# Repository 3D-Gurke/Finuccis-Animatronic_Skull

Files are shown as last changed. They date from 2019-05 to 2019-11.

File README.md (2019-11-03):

# 3D-Gurke
3D printable mechanic for animatronic skull (Halloween)

This project was inspired by  www.youtube.com/watch?v=b6z9ToMeCnw

When I found out, how expensive even only one animated skull including animatronic kits was, I decided to use my 3D printer 
to produce my own animatronic skull.
I live in Germany and I was unable to obtain the Lindberg skull in Europe, for which many animatronic kits are available.
Therefore, I looked for an available and cheap alternate skull an I found a skull model named XC-104, produced in China 
with worldwide availabilty. It is pretty heavy with its 1,2 kg but it works fine after some amendments.
Inside the skull a lot of material needs to be removed with a dremel tool. This takes about 1/2 hour and it is pretty messy.
If you accidently take away too much and you create a hole, who cares? 
It is supposed to be a rotten skull, ain't it?
Especially the material inside the skull from nose downward towards the upper jaw needs to be removed to make space for the eyes 
animatronic board. It needs to be fit in perfectly or it will interfere with the skull servo board. It is basically a press fit.
The lower jaw (mandible) is linked to the skull by two cable straps on each joint. I will include schematics.
The animatronic is commanded by a cheap Arduino nano clone from China. 4 EUR each. 
This special Arduino has one flaw though, if steering servos, the servos cannot run on the same power supply (directly) as the arduino.
Therefore a cheap voltage DC DC converter (<1 EUR) was used. The Arduino can run on 12V directly, the servos are running on 5V.
In this configuration, everything runs perfectly.
This project is still in progress, as especially the programming has not been done except for a small test program.
The programming must be on a time code to syncronise the movement of the jaw to any audio file. In my case: 3 skulls singing
the Ghotbusters song. Therefore I need to syncronise 3 skulls with one master Arduino which will be starting the 3 skulls syncronously
and will be also steering the sound file and lighting effects. This will be done in the future however.
I am an absolute beginner in programming ARDUINO and what I present here is mostly copied from various net sources. 
It works so far, but as the project is not finished as yet, it is far from perfection or even elegance, 
so do not massacre me for the imperfect code, please  !  :-)
Each skull must be individually tested on each servo for the physical movement limits- I will include the test program as well.
I used the cheapest servos available from China. Servo MG945 & SG90. These do not center correctly and every time you hit a specific angle defined in the program, the servos end up in another position near by. Absolute unacceptable if used in an RC model, for a project like this, they do okay.
I have not specifically calculated the cost of a complete skull, but I would estimate 1 skull with servos and Arduino to be 
below 100 EUR. 
A pretty attractive price for an animatronic 3 axis skull with RGB lighted 2 axis eyes.
All hole measures of the printable parts have been chosen small so you can drill the holes to the dimension you need.
This way you can easily convert from metric to imperial measure. For instance: The tube for the eyes servo board to connect to the center eye ball is 4mm or approximately 1/6 inch. You will have to drill the holes in the board and the center eye ball accordingly.

Video-Tutorials this project: https://www.youtube.com/watch?v=9NNKajxI0-s&list=PLTyc4D895PUEJc8eNipVYug8fxN45OCBS

Final Installation, as run on Oct 31st 2019 : https://www.youtube.com/watch?v=-8c9RkCJJGA

Please find all necessary files in the folders.

You may remix as you see fit. Have fun und viel Glück!

Glück auf!

3D-Gurke

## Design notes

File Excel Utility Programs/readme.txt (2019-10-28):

The Excel File "INO Change Code Generator" will help you to create and adjust the time line.
"Arduino Code Translator"  is a generic translator program to convert my Ghostbusters skull programs to your skull's limits.
"Arduino Code Translator_ALPHA" is the same program preset with the ALPHA skull time line.
"Arduino Code Translator_BETA" is the same program preset with the BETA skull time line.
"Arduino Code Translator_GAMMA" is the same program preset with the GAMMA skull time line.

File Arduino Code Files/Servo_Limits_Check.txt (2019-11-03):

#include <VarSpeedServo.h>
#include <Adafruit_NeoPixel.h>

// Servo 
VarSpeedServo servo1;   // NOD
VarSpeedServo servo2;   // SHAKE              
VarSpeedServo servo3;   // TILT
VarSpeedServo servo4;   // JAW
VarSpeedServo servo5;   // Eye X
VarSpeedServo servo6;   // Eye Y

const int servoPin1 = 3;
const int servoPin2 = 5;
const int servoPin3 = 6;
const int servoPin4 = 9;
const int servoPin5 = 10;
const int servoPin6 = 11;

// NeoPixel
#define PIN  2
#define NUMPIXELS 2
Adafruit_NeoPixel eyes = Adafruit_NeoPixel(NUMPIXELS, PIN, NEO_GRB + NEO_KHZ800);

void setup() 
{

eyes.begin();

// all servos 90°

servo1.attach(servoPin1);
servo1.write(90,30,false); 
servo2.attach(servoPin2);
servo2.write(90,30,false); 
servo3.attach(servoPin3);
servo3.write(90,30,false); 
servo4.attach(servoPin4);
servo4.write(90,30,false);
servo5.attach(servoPin5);
servo5.write(90,30,false); 
servo6.attach(servoPin6);
servo6.write(90,30,false); 

eyes.setPixelColor(0, eyes.Color(0,0,0));
eyes.setPixelColor(1, eyes.Color(0,0,0)); 
eyes.show();
}
void loop() 
{
eyes.setPixelColor(0, eyes.Color(0,100,0));
eyes.setPixelColor(1, eyes.Color(0,100,0)); 
eyes.show();
servo1.write(90,30,false);        // eyes light green when servo in 90° neutral
delay(3000);
eyes.setPixelColor(0, eyes.Color(100,0,0));
eyes.setPixelColor(1, eyes.Color(100,0,0)); 
eyes.show();
servo1.write(100,30,false);       // eyes light red when servo in tests limit
delay(3000);
eyes.setPixelColor(0, eyes.Color(0,100,0));
eyes.setPixelColor(1, eyes.Color(0,100,0)); 
eyes.show();
servo1.write(90,30,false);        // eyes light green when servo in 90° neutral
delay(3000);
eyes.setPixelColor(0, eyes.Color(100,0,0));
eyes.setPixelColor(1, eyes.Color(100,0,0)); 
eyes.show();
servo1.write(80,30,false);       // eyes light red when servo in tests limit
delay(3000);
eyes.setPixelColor(0, eyes.Color(0,100,0));
eyes.setPixelColor(1, eyes.Color(0,100,0)); 
eyes.show();
servo1.write(90,30,false);        // eyes light green when servo in 90° neutral

}

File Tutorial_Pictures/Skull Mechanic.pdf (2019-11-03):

### Aufbau der Anlenkmechanik für Halloween Totenkopf Schematic of linkage assembly for halloween skull

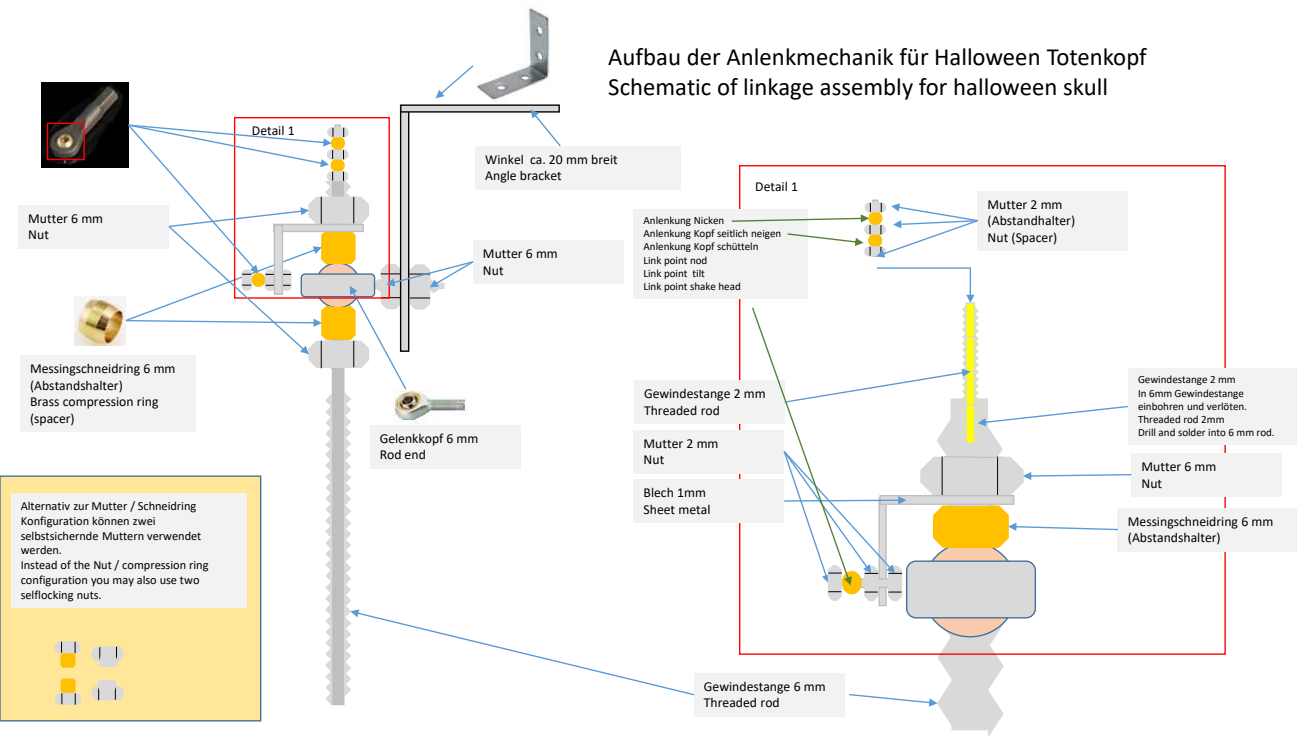
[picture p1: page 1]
Gewindestange 6 mm Threaded rod; Gelenkkopf 6 mm Rod end; Mutter 6 mm Nut; Detail 1; Mutter 2 mm Nut; Gewindestange 2 mm Threaded rod; Blech 1mm Sheet metal; Mutter 2 mm (Abstandhalter) Nut (Spacer); Messingschneidring 6 mm (Abstandshalter)

Winkel ca. 20 mm breit
Angle bracket

Anlenkung Nicken
Anlenkung Kopf seitlich neigen
Anlenkung Kopf schütteln
Link point nod
Link point tilt
Link point shake head

Messingschneidring 6 mm
(Abstandshalter)
Brass compression ring
(spacer)

Gewindestange 2 mm
In 6mm Gewindestange
einbohren und verlöten.
Threaded rod 2mm
Drill and solder into 6 mm rod.

Alternativ zur Mutter / Schneidring
Konfiguration können zwei
selbstsichernde Muttern verwendet
werden.
Instead of the Nut / compression ring
configuration you may also use two
selflocking nuts.

# Detail Anlenkung / Detail Linkage

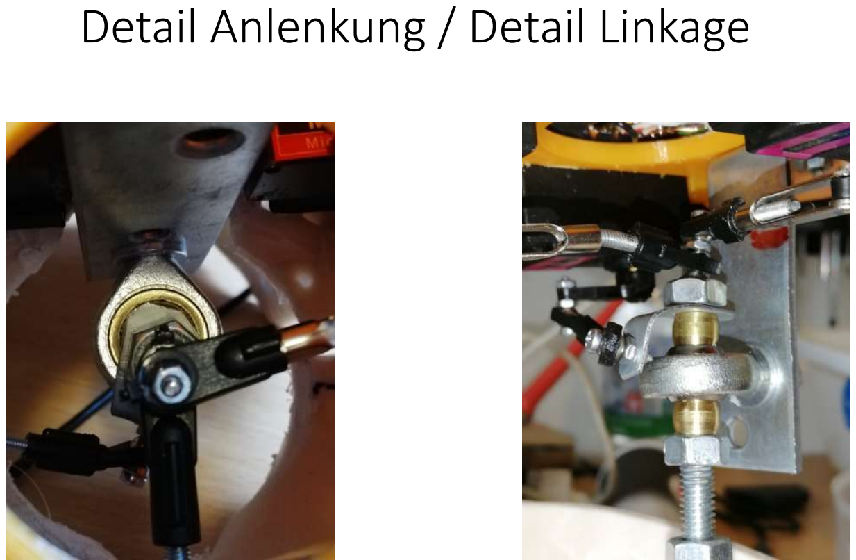
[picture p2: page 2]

### 19 x 15 x 21 cm , 1.16 kg Skull Medical Model XC-104 (China)

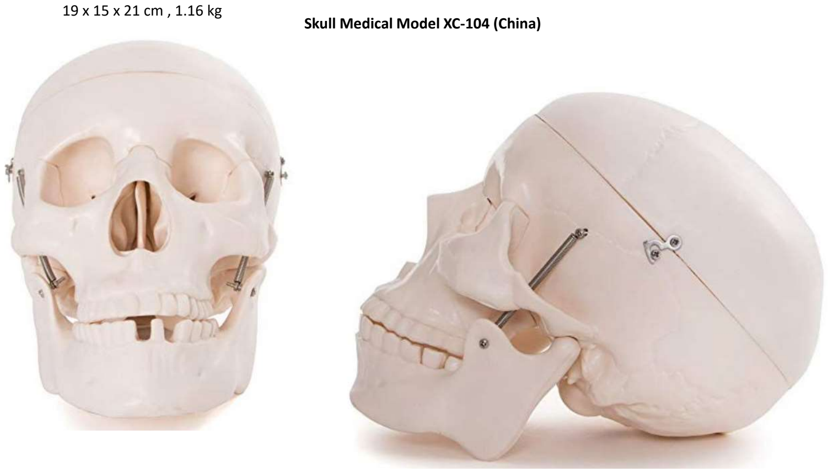
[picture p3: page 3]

# Servohalter Bestückung Servo board assembly

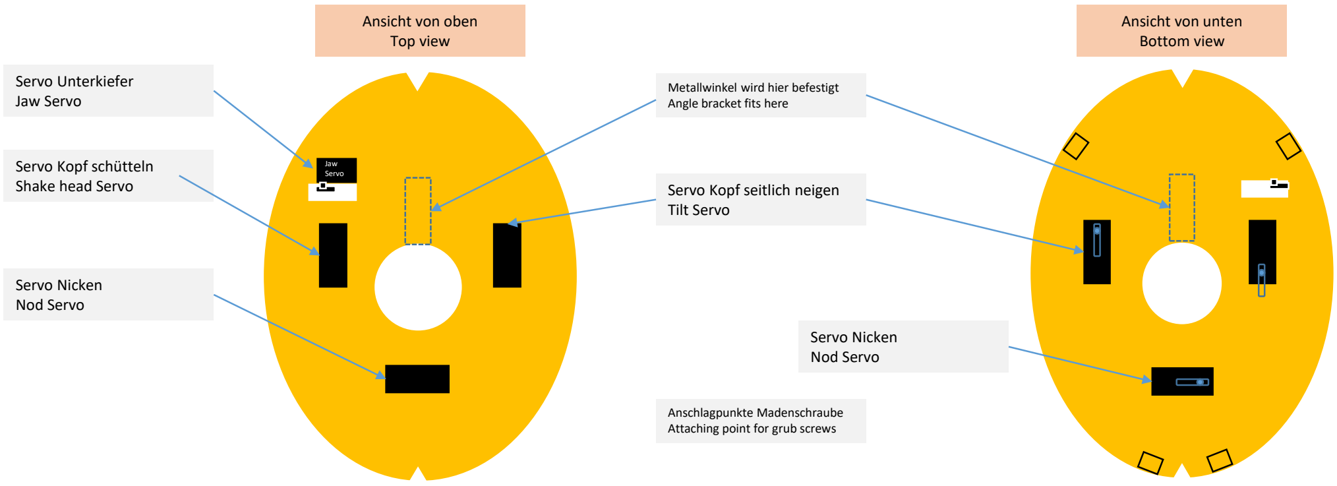
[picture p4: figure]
Jaw Servo; Servo Unterkiefer Jaw Servo; Servo Kopf schütteln Shake head Servo; Servo Nicken Nod Servo; Servo Kopf seitlich neigen Tilt Servo; Ansicht von oben Top view; Ansicht von unten Bottom view; Metallwinkel wird hier befestigt Angle bracket fits here; Anschlagpunkte Madenschraube Attaching point for grub screws

# Materialliste Skull

Schädel (Typ XC-104) | 1 stck | (Skull)
Skull Servo Board | 1 stck 3D Druck | (3D print)
Servo holder | 1 stck 3D Druck | (3D print)
Gewindestange 6 mm | 1 stck | (Threaded rod)
Gewindestange 2 mm | 3 stck | (Threaded rod)
Mutter 6 mm | 5 stck | (Nut)
Mutter 2 mm | 6 stck | (Nut)
Servo Kugelkopf 2 mm | 6 stck | (Servo link rod end)
Gelenkkopf m Gewindestange 6mm 1 stck | (Rod end)
Messingschneidring 6 mm | 2 stck oder 6 mm selbstsichernde Mutter 2 stck (Brass compression ring or 2 ea selflocking nut)
Metallwinkel 20 mm | 1 stck | (Angle bracket)
1 mm Blech | Reststück | (Sheet metal piece scrap)
Servo MG945 | 3 stck | (Servo, China ware)
Servo SG90 | 1 stck | (Servo, China ware)
Arduino USB Nano V3.0 | 1 stck | (Arduino)
Step-Down-Schaltregler | 2 stck | (Step down buck converter)
Lochrasterplatine (10 x 20 Löcher) | 1 stck | (Blank circuit board 10 by 20 holes)
Madenschraube 4mm | 4 stck | (Grub screw)

# Materialliste Eyes Board

Eyes Board: | 1 stck 3D Druck | (Eyes Board:, 3D print)
Eye Center Ball | 2 stck 3D Druck | (Eye Center Ball | , 3D print)
Eye Ball | 2 stck 3D Druck | (Eye Ball, 3D print)
Verbinder | 1 stck 3D Druck | (Link bar, 3D print)
Servo SG90 | 2 stck | (Servo, China ware)
Draht 1 mm | 10 cm | (Metal wire, 1 mm)
Rohr 4 mm aussen (z.B Plastik) | 10 cm | (Tube, 4 mm outer diameter plastic)
LED Typ WS2812 5050 (4 pin) | 2 stck | (LED, China ware)

2 mm Schrauben / Muttern / Unterlegscheiben / Kabelbinder / Steckverbinder / Lochrasterplatine / Kupferlackdraht
( 2mm screws / nuts / washers / cable straps / male & female pins for circuit boards / circuit board / magnet wire)

# Platine Oberseite / Circuit Board Top ViewZ 5V ¹²V LEDs Eyes

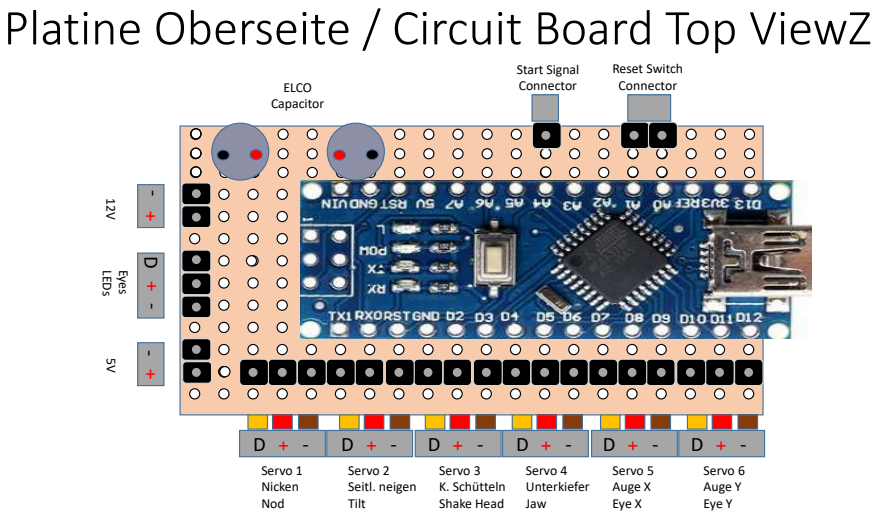
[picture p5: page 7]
Servo 1 Nicken Nod; Servo 2 Seitl. neigen Tilt; Servo 3 K. Schütteln Shake Head; Servo 4 Unterkiefer Jaw; Servo 5 Auge X Eye X; Servo 6 Auge Y Eye Y; Reset Switch Connector; Start Signal; ELCO; Connector; Capacitor

# Platine Oberseite / Circuit Board Top View

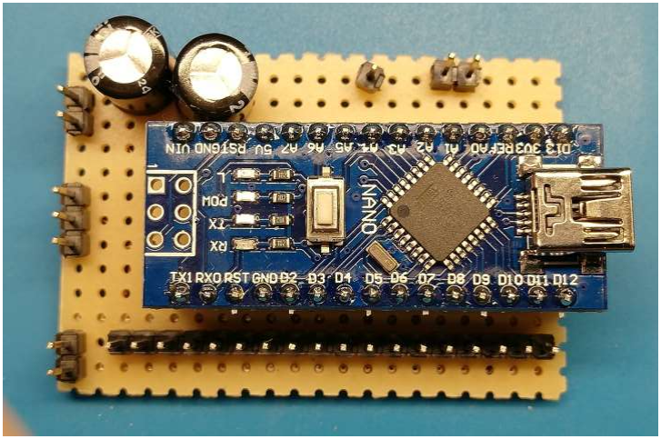
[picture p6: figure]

# Platine Unterseite/ CB Bottom View 5V 9V LEDs Eyes

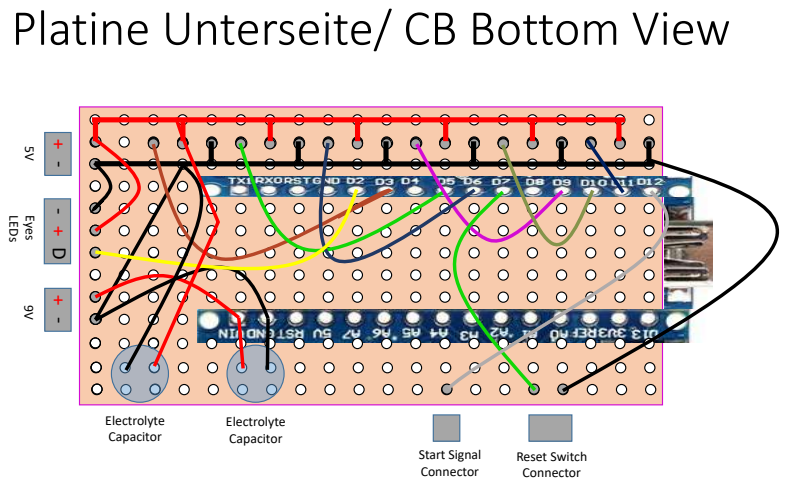
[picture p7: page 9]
Reset Switch Connector; Electrolyte Capacitor; Start Signal Connector

# Platine Unterseite/ CB Bottom View

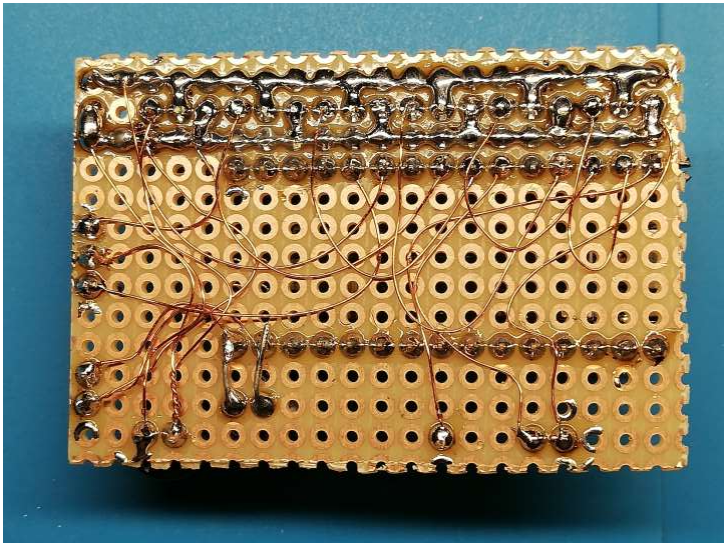
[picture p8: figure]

# Elektronische Schaltung Electronics Circuit

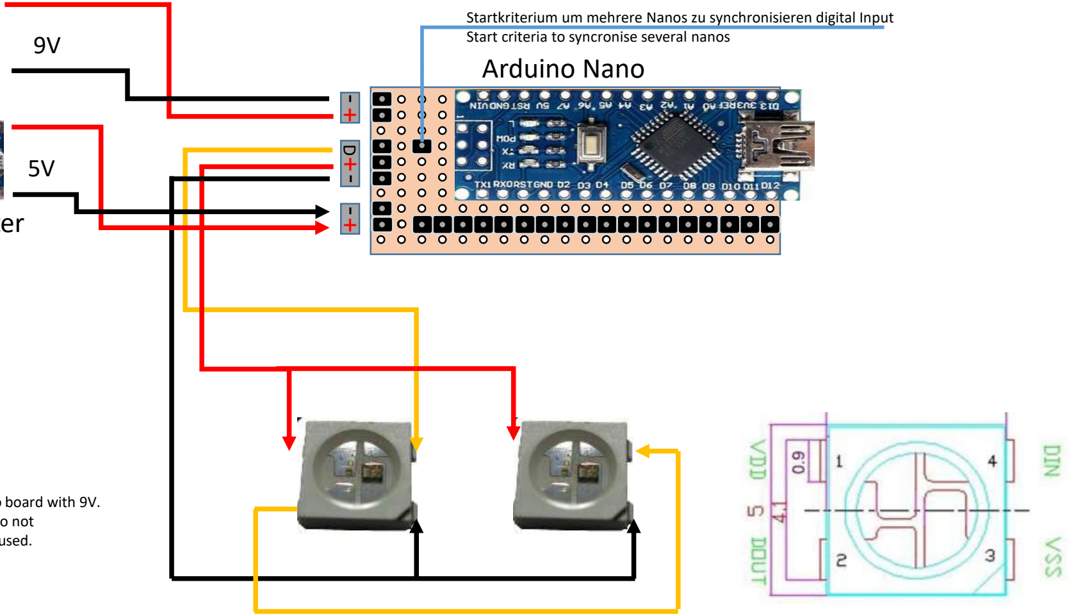
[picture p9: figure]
Arduino Nano

### Voltage Converter

Startkriterium um mehrere Nanos zu synchronisieren digital Input Start criteria to syncronise several nanos
Power Supply | 9V
12 V

Changed assembly:
Use a second step down voltage converter to power the Arduino board with 9V. When testing / programming, I found that some Arduino Nano do not
work correctly when only one step down voltage converter was used.
In this configuration, there were no more issues.

### Voltage Converter

!

# Servo Board Eyes/ Eye Board Assy

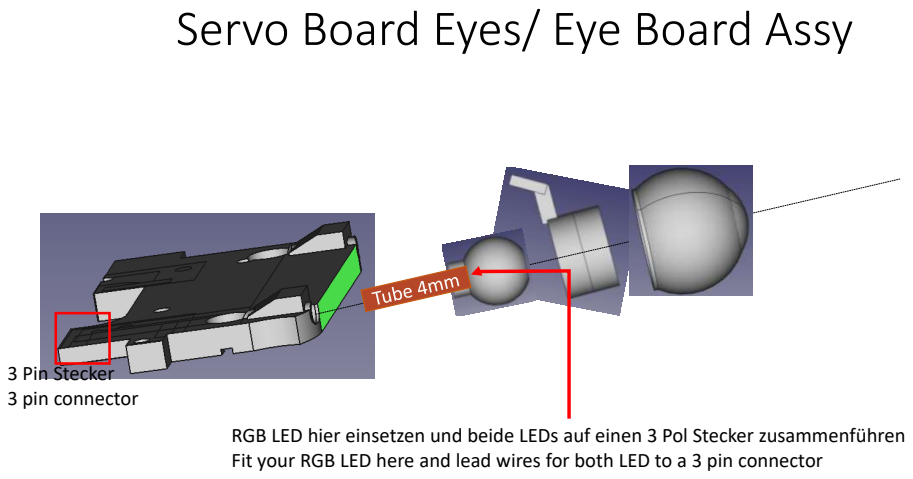
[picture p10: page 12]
3 Pin Stecker 3 pin connector

RGB LED hier einsetzen und beide LEDs auf einen 3 Pol Stecker zusammenführen
Fit your RGB LED here and lead wires for both LED to a 3 pin connector

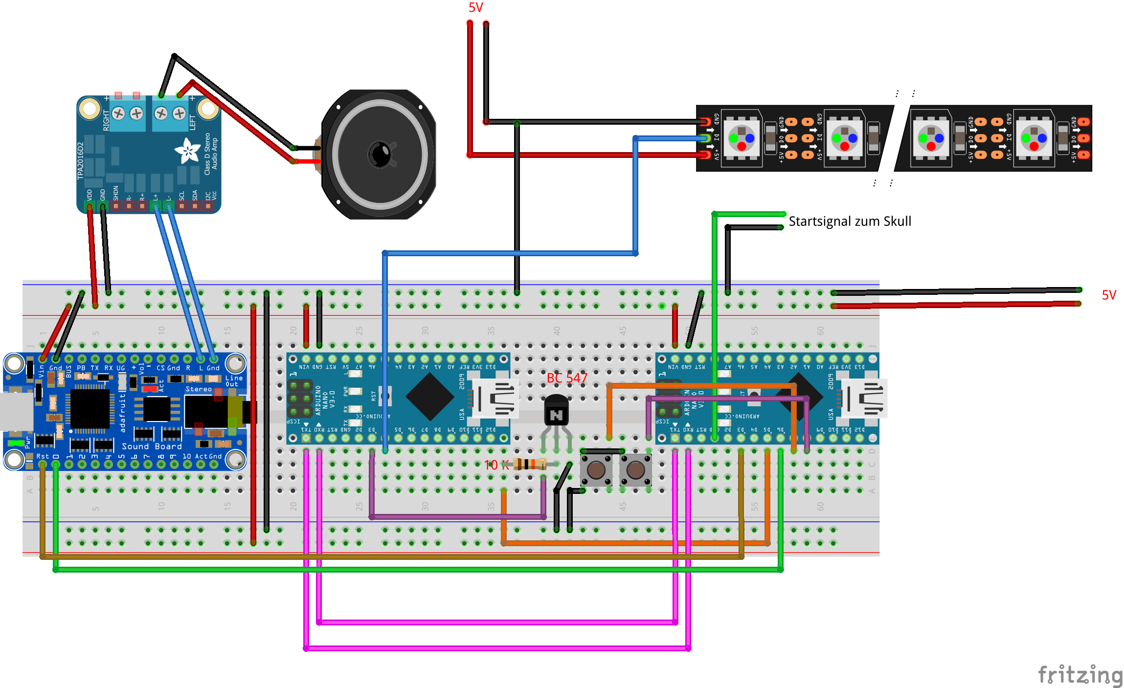
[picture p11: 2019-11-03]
Tutorial_Pictures/MASTER_BREAD_BOARD_schematic.png

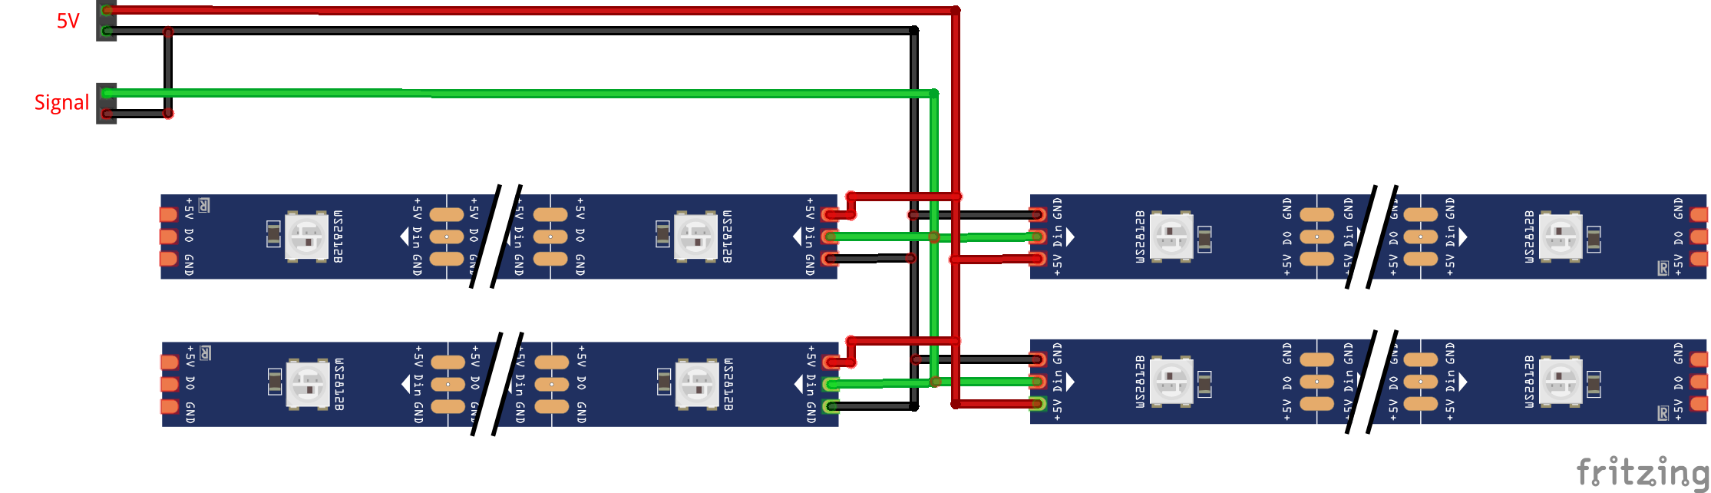
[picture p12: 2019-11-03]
Tutorial_Pictures/MASTER_LED_STRIP_schematic.png

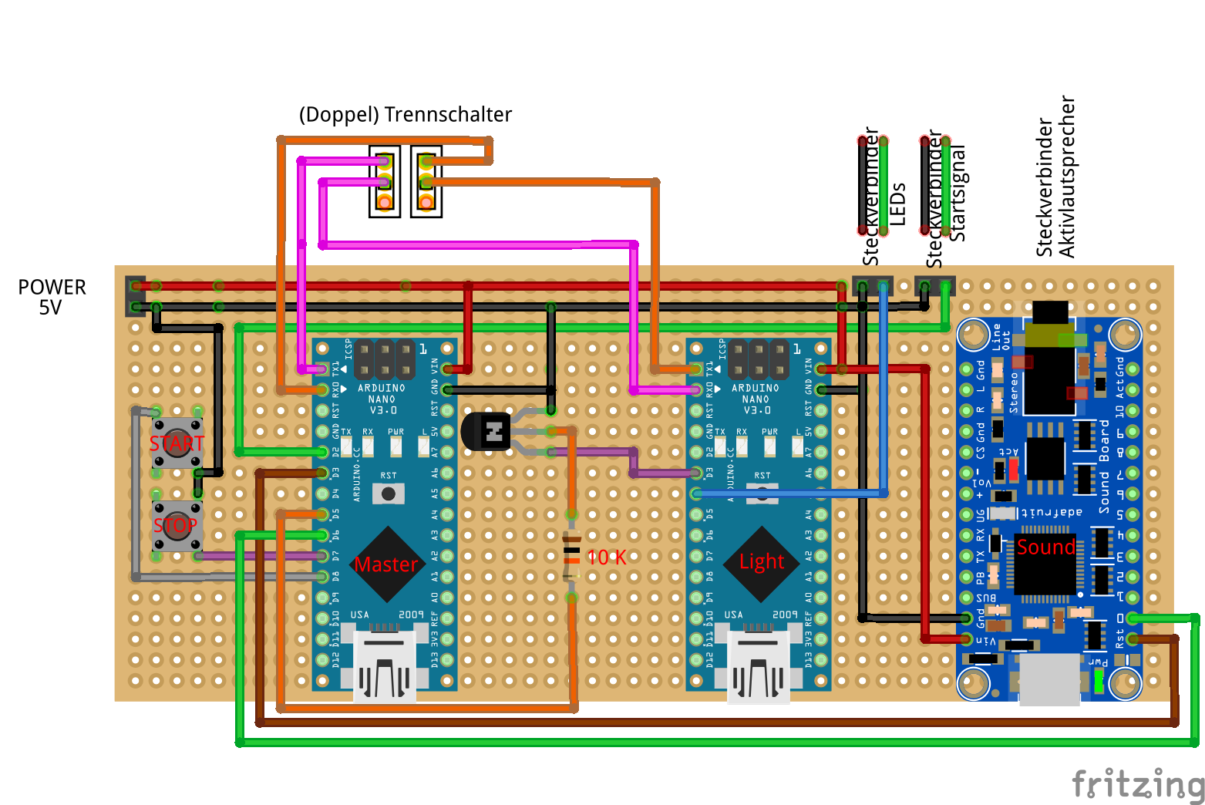
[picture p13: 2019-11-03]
Tutorial_Pictures/MASTER_PCB_schematic.png

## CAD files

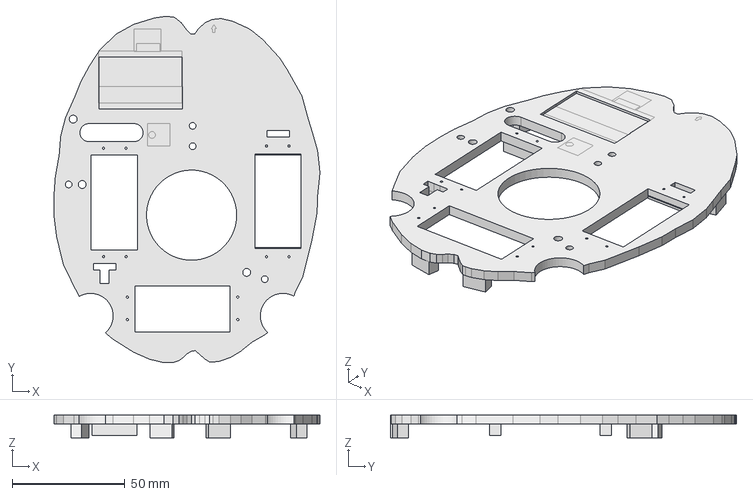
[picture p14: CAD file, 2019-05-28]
3D_Printables/Skull_Main_Board.FCStd
118.0 x 153.7 x 10.0 mm

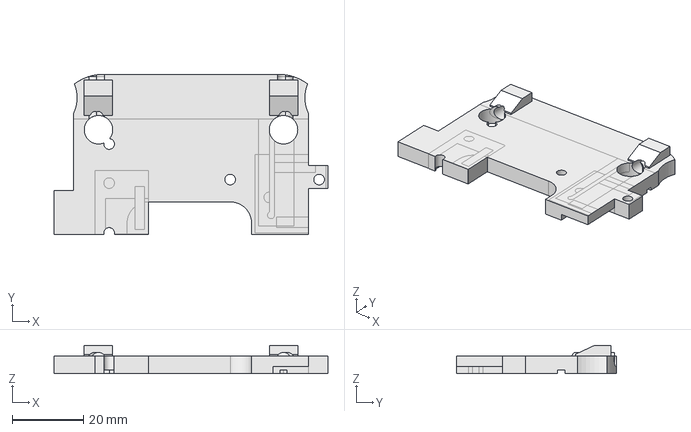
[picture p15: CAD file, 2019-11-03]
3D_Printables/Eyes_Servo_Board.FCStd
77.0 x 45.1 x 8.00 mm

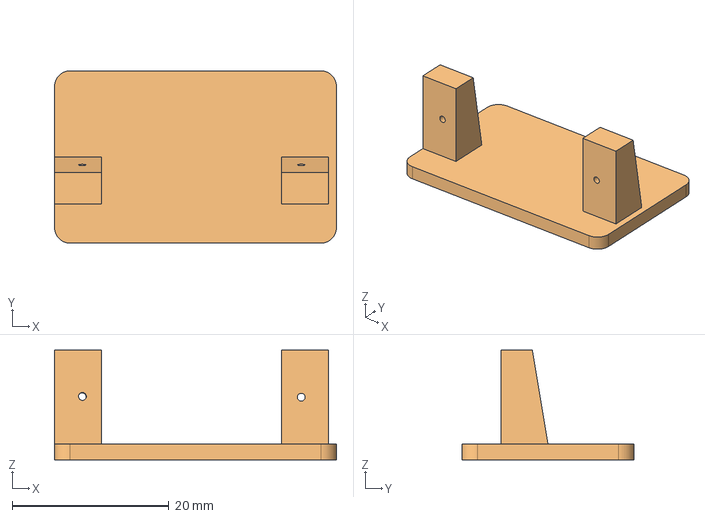
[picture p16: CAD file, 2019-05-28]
3D_Printables/Skull_Servo_Bracket_Jaw.FCStd
36.0 x 22.0 x 14.0 mm

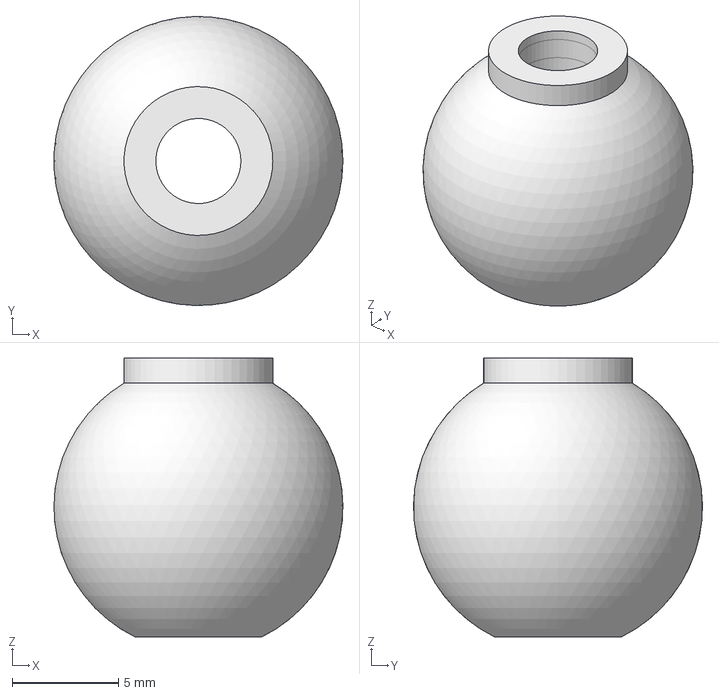
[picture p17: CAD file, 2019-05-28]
3D_Printables/Eyes_Centerball.FCStd
13.6 x 13.6 x 13.1 mm

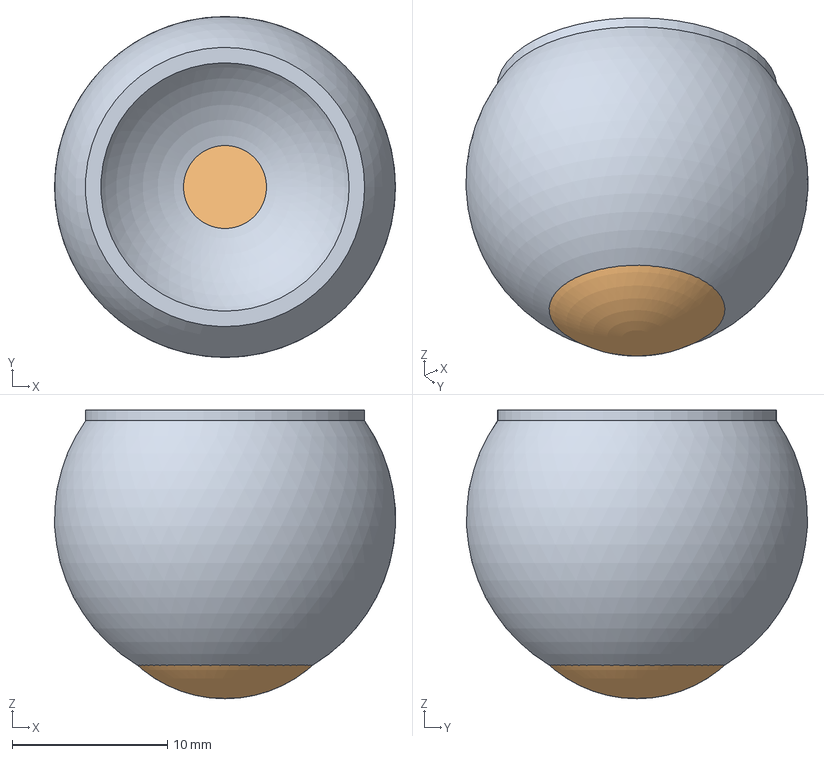
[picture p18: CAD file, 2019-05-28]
3D_Printables/Eyes_Eyeball_w_pupil.FCStd
22.0 x 22.0 x 18.6 mm

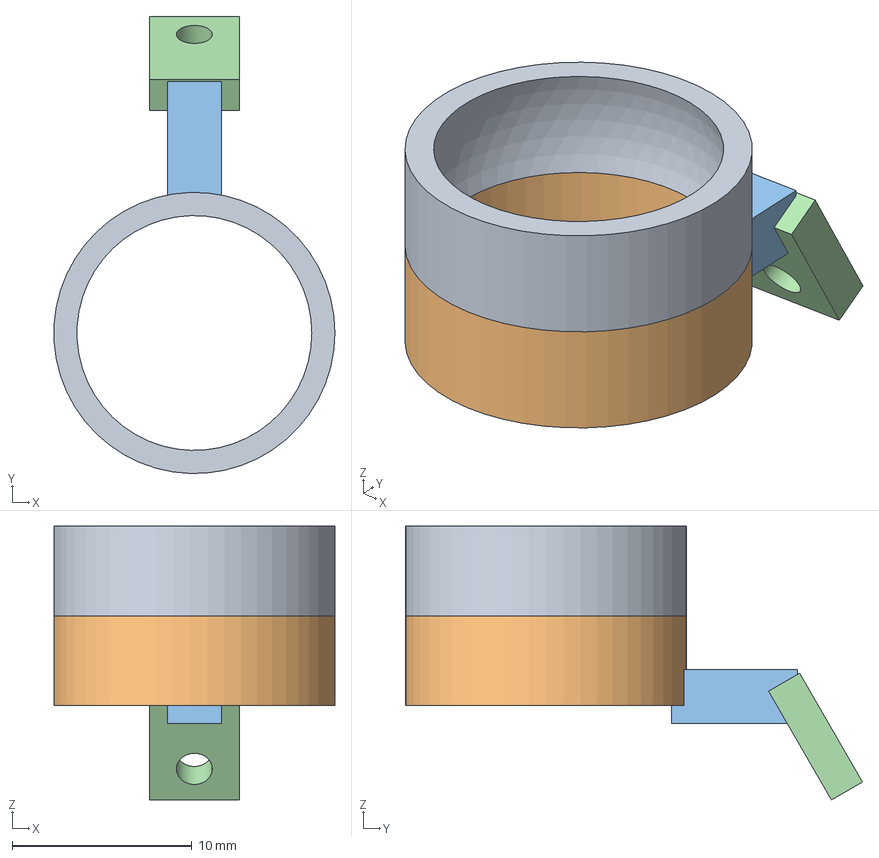
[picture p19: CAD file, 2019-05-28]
3D_Printables/Eyes_Snap_Ring_w_Lever.FCStd
15.6 x 25.5 x 15.3 mm
Würfel

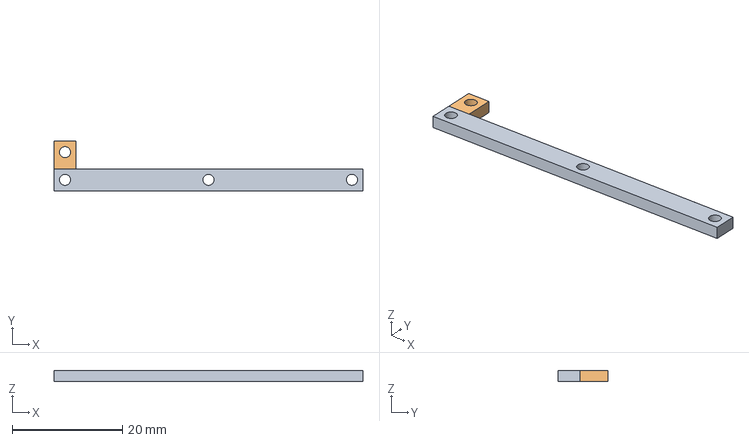
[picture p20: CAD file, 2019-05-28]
3D_Printables/Eyes_Lever_Connector.FCStd
56.0 x 9.00 x 2.00 mm

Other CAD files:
3D_Printables/Eyes_Centerball.stl
3D_Printables/Eyes_Eyeball_w_pupil.stl
3D_Printables/Eyes_Lever_Connector.stl
3D_Printables/Eyes_Servo_Board.stl
3D_Printables/Eyes_Snap_Ring_w_Lever.stl
3D_Printables/Skull_Main_Board.stl
3D_Printables/Skull_Servo_Bracket_Jaw.stl

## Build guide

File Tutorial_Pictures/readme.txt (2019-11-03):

Schematics. Please also watch the tutorials on youtube (playlist).

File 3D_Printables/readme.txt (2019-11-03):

Please find FreeCad-STD & STL files for 3D Print.

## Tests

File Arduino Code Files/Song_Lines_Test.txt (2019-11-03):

//  Servo Limits for DELTA SKULL

 // NOD  MAX UP 30   --MID 80--  MAX DOWN 110  
 // SHAKE  MAX STBD 50   --MID 98-- MAX PORT 145
// TILT  MAX STBD 130   --MID 95--  MAX PORT 50
// JAW  MAX OPEN 130   --MID 100--  MAX CLOSED 75    
// Eye X  MAX STBD 50 & Y70   --MID 95 --  MAX PORT 145  
// Eye Y  MAX UP 115   --MID 65 --  MAX Down 30

#include <VarSpeedServo.h>
#include <Adafruit_NeoPixel.h>

// Servo 
VarSpeedServo servo1;   // Nod
VarSpeedServo servo2;   // Shake
VarSpeedServo servo3;   // Tilt
VarSpeedServo servo4;   // Jaw
VarSpeedServo servo5;   // Eye X
VarSpeedServo servo6;   // Eye Y

const int servoPin1 = 3;
const int servoPin2 = 5;
const int servoPin3 = 6;
const int servoPin4 = 9;
const int servoPin5 = 10;
const int servoPin6 = 11;

// NeoPixel
#define PIN  2
#define NUMPIXELS 2
Adafruit_NeoPixel eyes = Adafruit_NeoPixel(NUMPIXELS, PIN, NEO_GRB + NEO_KHZ800);

void setup() 
{

eyes.begin(); // Initialisierung der NeoPixel

servo1.attach(servoPin1);
servo1.write(70,40,false);  // NOD  MAX UP 30   --MID 80--  MAX DOWN 110 
servo2.attach(servoPin2);
servo2.write(98,40,false); // SHAKE  MAX STBD 50   --MID 98-- MAX PORT 145
servo3.attach(servoPin3);
servo3.write(95,40,false); // TILT  MAX STBD 130   --MID 95--  MAX PORT 50
servo4.attach(servoPin4);
servo4.write(75,40,false); // JAW  MAX OPEN 130   --MID 100--  MAX CLOSED 75 
servo5.attach(servoPin5);
servo5.write(95,40,false); // Eye X  MAX STBD 50 & Y70   --MID 95 --  MAX PORT 145  
servo6.attach(servoPin6);
servo6.write(65,40,false); // Eye Y  MAX UP 115   --MID 65 --  MAX Down 30
delay(200);

//   Start of time coded action

    eyes.setPixelColor(0, eyes.Color(0,128,0)); // Eyes white to signal ready waiting for startsignal from Adafruit
    eyes.setPixelColor(1, eyes.Color(0,128,0)); // Eyes white to signal ready waiting for startsignal from Adafruit
    eyes.show(); // This sends the updated pixel color to the hardware.
}

void loop() 
{
// Eyes countdown from 3
    eyes.setPixelColor(0, eyes.Color(0,0,128)); 
    eyes.setPixelColor(1, eyes.Color(0,0,128)); 
    eyes.show(); 
    delay(100);
    eyes.setPixelColor(0, eyes.Color(0,0,0)); 
    eyes.setPixelColor(1, eyes.Color(0,0,0)); 
    eyes.show(); 
    delay(900);
    
    eyes.setPixelColor(0, eyes.Color(0,0,128)); 
    eyes.setPixelColor(1, eyes.Color(0,0,128)); 
    eyes.show(); 
    delay(100);
    eyes.setPixelColor(0, eyes.Color(0,0,0)); 
    eyes.setPixelColor(1, eyes.Color(0,0,0)); 
    eyes.show(); 
    delay(900);
    
    eyes.setPixelColor(0, eyes.Color(128,0,0)); 
    eyes.setPixelColor(1, eyes.Color(128,0,0)); 
    eyes.show(); 
    delay(100);
    eyes.setPixelColor(0, eyes.Color(0,0,0)); 
    eyes.setPixelColor(1, eyes.Color(0,0,0)); 
    eyes.show(); 
    delay(900);
    
    eyes.setPixelColor(0, eyes.Color(0,128,0)); 
    eyes.setPixelColor(1, eyes.Color(0,128,0)); 
    eyes.show(); 

 // JAW  MAX OPEN 130   --MID 100--  MAX CLOSED 75 

servo4.write(75,80,false); 
delay(100);
servo4.write(95,80,false); 
delay(100);
servo4.write(75,80,false);
delay(100);
servo4.write(95,80,false);  
delay(100);
servo4.write(75,80,false);
delay(100);
servo4.write(105,80,false); 
delay(200);
servo4.write(75,80,false);
delay(100);
servo4.write(95,80,false);  
delay(100);
servo4.write(75,80,false);
delay(100);
servo4.write(110,80,false);  
delay(400);
servo4.write(75,80,false);

delay(3000);
        
eyes.setPixelColor(0, eyes.Color(0,0,0)); 
eyes.setPixelColor(1, eyes.Color(0,0,0)); 
eyes.show(); 
delay(1000);
 
}

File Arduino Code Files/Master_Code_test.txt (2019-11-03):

// Test version- runs only one time line, resets and waits for start button. Stop switch resets immediately.

//  Light Codes

//  1  FadeInOut - Color (red, green. blue)
//  2  STROBE WHITE     
//  3  Strobe - Color (red, green, blue), number of flashes, flash speed, end pause
//  4  Twinkle - Color
//  5  TWINKLE  TwinkleRandom 
//  6  Running Lights - Color (red, green, blue), wave dealy
//  7  Sparkle - Color (red, green, blue), speed delay
//  8  Running Lights - RED WHITE BLUE
//  10 rainbowCycle
//  11 theatherChase red
//  12 theatherChase - RAINBOW  (red, green, blue), speed delay
//  13 Fire(55,120,15);    theaterChaseRainbow - 
//  14 meteorRain -WHITE
//  15 Centerspot()
//  16 Outspot()
//  17 SLOWStrobe - MultiColor
//  18 meteorRain -PINK
//  19 meteorRain -GREEN
//  20 Snow Sparkle

#include <SoftwareSerial.h>

// inputs and outputs 
const int STARTBAND = 2;                    // Start the band of slave skulls                   
const int RESETSFX = 3;                     // Reset soundboard
const int LIGHTSOFF = 5;                    // Reset lights slave arduino to off
const int PLAY1 = 6;                        // Start soundboard
const int STOPSWITCH = 7;                   // Stopswitch
const int STARTSWITCH = 8;                  // Startswitch
const int INDICATOR = 12;                   // Optional Indicator for testing
unsigned long runtime;          
unsigned long offsetMillis;

void setup () {
// set the modes for the switches / pins
  pinMode(STARTSWITCH, INPUT_PULLUP);
  pinMode(STOPSWITCH, INPUT_PULLUP);
  pinMode(PLAY1, OUTPUT);
  pinMode(RESETSFX, OUTPUT);
  pinMode(STARTBAND, OUTPUT);
  pinMode(LIGHTSOFF, OUTPUT);
  pinMode(INDICATOR, OUTPUT);

// Preset Pin Signals
  digitalWrite(STARTBAND, HIGH);      // Activates slave skulls when LOW
  digitalWrite(RESETSFX, HIGH);       // Resets sound board when LOW
  digitalWrite(PLAY1, HIGH);          // Activates sound board when LOW
  digitalWrite(LIGHTSOFF, LOW);       // Triggers lights off on lights slave when HIGH (through transistor)
  digitalWrite(INDICATOR, HIGH);      // Optional indicator for testing     

// Serial COM setup
  Serial.begin(9600);
  Serial.setTimeout(10);

// Start Switch Option (for testing and programming) - will not be used in continuous play mode    
  while (digitalRead(STARTSWITCH) == HIGH) {}
  offsetMillis = millis();

}   // void setup

void loop() 
{

  runtime=millis();
  
  digitalWrite(INDICATOR, LOW); // shows when loop gets active (optional)

// Stop switch action for testing / programming purposes - will not be used in continuous play mode
  
  if (digitalRead(STOPSWITCH) == LOW) 
  {
    digitalWrite(RESETSFX, LOW);
    RSTLT();
    delay(200);
    digitalWrite(RESETSFX, HIGH); setup();
  }

if ((runtime-offsetMillis) >=    3000 && (runtime-offsetMillis) <=    3003) {digitalWrite (STARTBAND,LOW);}
if ((runtime-offsetMillis) >=    3200 && (runtime-offsetMillis) <=    3203) {digitalWrite (STARTBAND,HIGH);}
if ((runtime-offsetMillis) >=    4200 && (runtime-offsetMillis) <=    4203) {digitalWrite (PLAY1, LOW);}
if ((runtime-offsetMillis) >=    4700 && (runtime-offsetMillis) <=    4703) {digitalWrite (PLAY1, HIGH);}

if ((runtime-offsetMillis) >=    6721 && (runtime-offsetMillis) <=    6724) { RSTLT(); delay(6);Serial.print(13);delay(5); }               // Beat 1  TWINKLE COLOR
if ((runtime-offsetMillis) >=    7241 && (runtime-offsetMillis) <=    7244) { }               // Beat 2
if ((runtime-offsetMillis) >=    7762 && (runtime-offsetMillis) <=    7765) { }               // Beat 3
if ((runtime-offsetMillis) >=    8282 && (runtime-offsetMillis) <=    8285) { }               // Beat 4
if ((runtime-offsetMillis) >=    8803 && (runtime-offsetMillis) <=    8806) { }               // Beat 5
if ((runtime-offsetMillis) >=    9324 && (runtime-offsetMillis) <=    9327) { }               // Beat 6
if ((runtime-offsetMillis) >=    9844 && (runtime-offsetMillis) <=    9847) { }               // Beat 7
if ((runtime-offsetMillis) >=   10365 && (runtime-offsetMillis) <=   10368) { }               // Beat 8
if ((runtime-offsetMillis) >=   10885 && (runtime-offsetMillis) <=   10888) { }               // Beat 9
if ((runtime-offsetMillis) >=   11406 && (runtime-offsetMillis) <=   11409) { }               // Beat 10
if ((runtime-offsetMillis) >=   11927 && (runtime-offsetMillis) <=   11930) { }               // Beat 11
if ((runtime-offsetMillis) >=   12447 && (runtime-offsetMillis) <=   12450) { }               // Beat 12
if ((runtime-offsetMillis) >=   12968 && (runtime-offsetMillis) <=   12971) { }               // Beat 13
if ((runtime-offsetMillis) >=   13488 && (runtime-offsetMillis) <=   13491) { }               // Beat 14
if ((runtime-offsetMillis) >=   14009 && (runtime-offsetMillis) <=   14012) { }               // Beat 15
if ((runtime-offsetMillis) >=   14530 && (runtime-offsetMillis) <=   14533) { }               // Beat 16
if ((runtime-offsetMillis) >=   15050 && (runtime-offsetMillis) <=   15053) { RSTLT(); delay(6);Serial.print(3);delay(5);}               // Beat 17
if ((runtime-offsetMillis) >=   15571 && (runtime-offsetMillis) <=   15574) { }               // Beat 18
if ((runtime-offsetMillis) >=   16091 && (runtime-offsetMillis) <=   16094) { }                 // Beat 19
if ((runtime-offsetMillis) >=   16612 && (runtime-offsetMillis) <=   16615) { }               // Beat 20
if ((runtime-offsetMillis) >=   17133 && (runtime-offsetMillis) <=   17136) { RSTLT(); delay(6);Serial.print(12);delay(5); }               // Beat 21
if ((runtime-offsetMillis) >=   17653 && (runtime-offsetMillis) <=   17656) { }               // Beat 22
if ((runtime-offsetMillis) >=   18174 && (runtime-offsetMillis) <=   18177) { }               // Beat 23
if ((runtime-offsetMillis) >=   18694 && (runtime-offsetMillis) <=   18697) { }               // Beat 24
if ((runtime-offsetMillis) >=   19215 && (runtime-offsetMillis) <=   19218) { }               // Beat 25
if ((runtime-offsetMillis) >=   19736 && (runtime-offsetMillis) <=   19739) { }               // Beat 26
if ((runtime-offsetMillis) >=   20256 && (runtime-offsetMillis) <=   20259) { }               // Beat 27
if ((runtime-offsetMillis) >=   20777 && (runtime-offsetMillis) <=   20780) { }               // Beat 28
if ((runtime-offsetMillis) >=   21297 && (runtime-offsetMillis) <=   21300) { }               // Beat 29
if ((runtime-offsetMillis) >=   21818 && (runtime-offsetMillis) <=   21821) { }               // Beat 30
if ((runtime-offsetMillis) >=   22339 && (runtime-offsetMillis) <=   22342) { }               // Beat 31
if ((runtime-offsetMillis) >=   22859 && (runtime-offsetMillis) <=   22862) { }               // Beat 32
if ((runtime-offsetMillis) >=   23380 && (runtime-offsetMillis) <=   23383) { }               // Beat 33
if ((runtime-offsetMillis) >=   23900 && (runtime-offsetMillis) <=   23903) { }               // Beat 34
if ((runtime-offsetMillis) >=   24421 && (runtime-offsetMillis) <=   24424) { }               // Beat 35
if ((runtime-offsetMillis) >=   24942 && (runtime-offsetMillis) <=   24945) { }               // Beat 36
if ((runtime-offsetMillis) >=   25462 && (runtime-offsetMillis) <=   25465) { RSTLT(); delay(6);Serial.print(10);delay(5); }                // Beat 37  RAINBOW CYCLE
if ((runtime-offsetMillis) >=   25983 && (runtime-offsetMillis) <=   25986) { }               // Beat 38
if ((runtime-offsetMillis) >=   26503 && (runtime-offsetMillis) <=   26506) { }               // Beat 39
if ((runtime-offsetMillis) >=   27024 && (runtime-offsetMillis) <=   27027) { }               // Beat 40
if ((runtime-offsetMillis) >=   27545 && (runtime-offsetMillis) <=   27548) { }               // Beat 41
if ((runtime-offsetMillis) >=   28065 && (runtime-offsetMillis) <=   28068) { }               // Beat 42
if ((runtime-offsetMillis) >=   28586 && (runtime-offsetMillis) <=   28589) { }               // Beat 43
if ((runtime-offsetMillis) >=   29106 && (runtime-offsetMillis) <=   29109) { }               // Beat 44
if ((runtime-offsetMillis) >=   29627 && (runtime-offsetMillis) <=   29630) { }               // Beat 45
if ((runtime-offsetMillis) >=   30148 && (runtime-offsetMillis) <=   30151) { }               // Beat 46
if ((runtime-offsetMillis) >=   30668 && (runtime-offsetMillis) <=   30671) { }               // Beat 47   
if ((runtime-offsetMillis) >=   31189 && (runtime-offsetMillis) <=   31192) { RSTLT(); delay(6);Serial.print(16);delay(5); }               // Beat 48  OUTSPOT
if ((runtime-offsetMillis) >=   31709 && (runtime-offsetMillis) <=   31712) { }               // Beat 49  
if ((runtime-offsetMillis) >=   32230 && (runtime-offsetMillis) <=   32233) { RSTLT(); delay(6);Serial.print(14);delay(5); }                // Beat 50 Meteorrain White 
if ((runtime-offsetMillis) >=   32751 && (runtime-offsetMillis) <=   32754) { }               // Beat 51
if ((runtime-offsetMillis) >=   33271 && (runtime-offsetMillis) <=   33274) { RSTLT(); delay(6);Serial.print(15);delay(5); }              // Beat 52  CENTERSPOT
if ((runtime-offsetMillis) >=   33792 && (runtime-offsetMillis) <=   33795) { }               // Beat 53
if ((runtime-offsetMillis) >=   34312 && (runtime-offsetMillis) <=   34315) { RSTLT(); delay(6);Serial.print(19);delay(5); }              // Beat 54  Meteorrain green 
if ((runtime-offsetMillis) >=   34833 && (runtime-offsetMillis) <=   34836) { }               // Beat 55
if ((runtime-offsetMillis) >=   35354 && (runtime-offsetMillis) <=   35357) { RSTLT(); delay(6);Serial.print(15);delay(5); }               // Beat 56  CENTERSPOT
if ((runtime-offsetMillis) >=   35874 && (runtime-offsetMillis) <=   35877) { }               // Beat 57
if ((runtime-offsetMillis) >=   36395 && (runtime-offsetMillis) <=   36398) { }               // Beat 58 
if ((runtime-offsetMillis) >=   36915 && (runtime-offsetMillis) <=   36918) { RSTLT(); delay(6);Serial.print(18);delay(5); }              // Beat 59 Meteorrain PINK 
if ((runtime-offsetMillis) >=   37436 && (runtime-offsetMillis) <=   37439) { }                // Beat 60
if ((runtime-offsetMillis) >=   37957 && (runtime-offsetMillis) <=   37960) { RSTLT(); delay(6);Serial.print(15);delay(5); }             // Beat 61  CENTERSPOT 
if ((runtime-offsetMillis) >=   38477 && (runtime-offsetMillis) <=   38480) { }               // Beat 62
if ((runtime-offsetMillis) >=   38998 && (runtime-offsetMillis) <=   39001) { }                // Beat 63
if ((runtime-offsetMillis) >=   39518 && (runtime-offsetMillis) <=   39521) { RSTLT(); delay(6);Serial.print(16);delay(5); }              // Beat 64  OUTSPOT
if ((runtime-offsetMillis) >=   40039 && (runtime-offsetMillis) <=   40042) { }               // Beat 65 
if ((runtime-offsetMillis) >=   40560 && (runtime-offsetMillis) <=   40563) { RSTLT(); delay(6);Serial.print(3);delay(5); }                // Beat 66 STROBE COLOR
if ((runtime-offsetMillis) >=   41080 && (runtime-offsetMillis) <=   41083) { }               // Beat 67
if ((runtime-offsetMillis) >=   41601 && (runtime-offsetMillis) <=   41604) { RSTLT(); delay(6);Serial.print(15);delay(5); }              // Beat 68 CENTERSPOT
if ((runtime-offsetMillis) >=   42121 && (runtime-offsetMillis) <=   42124) { }                // Beat 69
if ((runtime-offsetMillis) >=   42642 && (runtime-offsetMillis) <=   42645) { }                // Beat 70 
if ((runtime-offsetMillis) >=   43163 && (runtime-offsetMillis) <=   43166) { RSTLT(); delay(6);Serial.print(3);delay(5); }               // Beat 71  STROBE COLOR
if ((runtime-offsetMillis) >=   43683 && (runtime-offsetMillis) <=   43686) { RSTLT(); delay(6);Serial.print(15);delay(5); }               // Beat 72  CENTERSPOT
if ((runtime-offsetMillis) >=   44204 && (runtime-offsetMillis) <=   44207) { }              // Beat 73
if ((runtime-offsetMillis) >=   44724 && (runtime-offsetMillis) <=   44727) { }               // Beat 74  
if ((runtime-offsetMillis) >=   45245 && (runtime-offsetMillis) <=   45248) { RSTLT(); delay(6);Serial.print(3);delay(5); }                // Beat 75  STROBE COLOR
if ((runtime-offsetMillis) >=   45766 && (runtime-offsetMillis) <=   45769) { }               // Beat 76
if ((runtime-offsetMillis) >=   46286 && (runtime-offsetMillis) <=   46289) { RSTLT(); delay(6);Serial.print(15);delay(5); }                  // Beat 77  CENTERSPOT
if ((runtime-offsetMillis) >=   46807 && (runtime-offsetMillis) <=   46810) { }               // Beat 78
if ((runtime-offsetMillis) >=   47327 && (runtime-offsetMillis) <=   47330) { RSTLT(); delay(6);Serial.print(19);delay(5); }               // Beat 79  Meteorrain green 
if ((runtime-offsetMillis) >=   47848 && (runtime-offsetMillis) <=   47851) { RSTLT(); delay(6);Serial.print(16);delay(5); }               // Beat 80  OUTSPOT
if ((runtime-offsetMillis) >=   48369 && (runtime-offsetMillis) <=   48372) { }               // Beat 81
if ((runtime-offsetMillis) >=   48889 && (runtime-offsetMillis) <=   48892) { }               // Beat 82
if ((runtime-offsetMillis) >=   49410 && (runtime-offsetMillis) <=   49413) { RSTLT(); delay(6);Serial.print(3);delay(5); }                // Beat 83  STROBE COLOR 
if ((runtime-offsetMillis) >=   49930 && (runtime-offsetMillis) <=   49933) { }               // Beat 84
if ((runtime-offsetMillis) >=   50451 && (runtime-offsetMillis) <=   50454) { RSTLT(); delay(6);Serial.print(10);delay(5); }                 // Beat 85   RAINBOW CYCLE
if ((runtime-offsetMillis) >=   50972 && (runtime-offsetMillis) <=   50975) { }               // Beat 86
if ((runtime-offsetMillis) >=   51492 && (runtime-offsetMillis) <=   51495) { }               // Beat 87
if ((runtime-offsetMillis) >=   52013 && (runtime-offsetMillis) <=   52016) { }               // Beat 88
if ((runtime-offsetMillis) >=   52533 && (runtime-offsetMillis) <=   52536) { }               // Beat 89
if ((runtime-offsetMillis) >=   53054 && (runtime-offsetMillis) <=   53057) { }               // Beat 90
if ((runtime-offsetMillis) >=   53575 && (runtime-offsetMillis) <=   53578) { }               // Beat 91
if ((runtime-offsetMillis) >=   54095 && (runtime-offsetMillis) <=   54098) { }               // Beat 92
if ((runtime-offsetMillis) >=   54616 && (runtime-offsetMillis) <=   54619) { }               // Beat 93
if ((runtime-offsetMillis) >=   55136 && (runtime-offsetMillis) <=   55139) { }               // Beat 94
if ((runtime-offsetMillis) >=   55657 && (runtime-offsetMillis) <=   55660) { }               // Beat 95
if ((runtime-offsetMillis) >=   56178 && (runtime-offsetMillis) <=   56181) { }               // Beat 96
if ((runtime-offsetMillis) >=   56698 && (runtime-offsetMillis) <=   56701) { RSTLT(); delay(6);Serial.print(15);delay(5); }                 // Beat 97  CENTERSPOT
if ((runtime-offsetMillis) >=   57219 && (runtime-offsetMillis) <=   57222) { }               // Beat 98
if ((runtime-offsetMillis) >=   57739 && (runtime-offsetMillis) <=   57742) { }               // Beat 99
if ((runtime-offsetMillis) >=   58260 && (runtime-offsetMillis) <=   58263) { RSTLT(); delay(6);Serial.print(10);delay(5); }                  // Beat 100  RAINBOW CYCLE
if ((runtime-offsetMillis) >=   58781 && (runtime-offsetMillis) <=   58784) { }               // Beat 101
if ((runtime-offsetMillis) >=   59301 && (runtime-offsetMillis) <=   59304) { }               // Beat 102
if ((runtime-offsetMillis) >=   59822 && (runtime-offsetMillis) <=   59825) { }               // Beat 103
if ((runtime-offsetMillis) >=   60342 && (runtime-offsetMillis) <=   60345) { }               // Beat 104
if ((runtime-offsetMillis) >=   60863 && (runtime-offsetMillis) <=   60866) { }               // Beat 105
if ((runtime-offsetMillis) >=   61384 && (runtime-offsetMillis) <=   61387) { }               // Beat 106
if ((runtime-offsetMillis) >=   61904 && (runtime-offsetMillis) <=   61907) { }               // Beat 107
if ((runtime-offsetMillis) >=   62425 && (runtime-offsetMillis) <=   62428) { }               // Beat 108
if ((runtime-offsetMillis) >=   62945 && (runtime-offsetMillis) <=   62948) { }               // Beat 109
if ((runtime-offsetMillis) >=   63466 && (runtime-offsetMillis) <=   63469) { }               // Beat 110
if ((runtime-offsetMillis) >=   63987 && (runtime-offsetMillis) <=   63990) { }               // Beat 111
if ((runtime-offsetMillis) >=   64507 && (runtime-offsetMillis) <=   64510) { }               // Beat 112
if ((runtime-offsetMillis) >=   65028 && (runtime-offsetMillis) <=   65031) { RSTLT(); delay(6);Serial.print(15);delay(5); }                 // Beat 113  CENTERSPOT  
if ((runtime-offsetMillis) >=   65548 && (runtime-offsetMillis) <=   65551) { }               // Beat 114
if ((runtime-offsetMillis) >=   66069 && (runtime-offsetMillis) <=   66072) { RSTLT(); delay(6);Serial.print(2);delay(5);}               // Beat 115  STROBE WHITE
if ((runtime-offsetMillis) >=   66590 && (runtime-offsetMillis) <=   66593) {   }               // Beat 116   
if ((runtime-offsetMillis) >=   67110 && (runtime-offsetMillis) <=   67113) { RSTLT(); delay(6);Serial.print(10);delay(5); }                 // Beat 117  RAINBOW CYCLE
if ((runtime-offsetMillis) >=   67631 && (runtime-offsetMillis) <=   67634) { }               // Beat 118
if ((runtime-offsetMillis) >=   68151 && (runtime-offsetMillis) <=   68154) { }               // Beat 119
if ((runtime-offsetMillis) >=   68672 && (runtime-offsetMillis) <=   68675) { }               // Beat 120
if ((runtime-offsetMillis) >=   69193 && (runtime-offsetMillis) <=   69196) { }               // Beat 121
if ((runtime-offsetMillis) >=   69713 && (runtime-offsetMillis) <=   69716) { }               // Beat 122
if ((runtime-offsetMillis) >=   70234 && (runtime-offsetMillis) <=   70237) { }               // Beat 123
if ((runtime-offsetMillis) >=   70754 && (runtime-offsetMillis) <=   70757) { }               // Beat 124
if ((runtime-offsetMillis) >=   71275 && (runtime-offsetMillis) <=   71278) { }               // Beat 125
if ((runtime-offsetMillis) >=   71796 && (runtime-offsetMillis) <=   71799) { }               // Beat 126
if ((runtime-offsetMillis) >=   72316 && (runtime-offsetMillis) <=   72319) { }               // Beat 127
if ((runtime-offsetMillis) >=   72837 && (runtime-offsetMillis) <=   72840) { }               // Beat 128
if ((runtime-offsetMillis) >=   73357 && (runtime-offsetMillis) <=   73360) { }               // Beat 129
if ((runtime-offsetMillis) >=   73878 && (runtime-offsetMillis) <=   73881) { }               // Beat 130
if ((runtime-offsetMillis) >=   74399 && (runtime-offsetMillis) <=   74402) { }               // Beat 131
if ((runtime-offsetMillis) >=   74919 && (runtime-offsetMillis) <=   74922) { RSTLT(); delay(6);Serial.print(15);delay(5); }                 // Beat 132  CENTERSPOT
if ((runtime-offsetMillis) >=   75440 && (runtime-offsetMillis) <=   75443) { }               // Beat 133
if ((runtime-offsetMillis) >=   75960 && (runtime-offsetMillis) <=   75963) { }               // Beat 134
if ((runtime-offsetMillis) >=   76481 && (runtime-offsetMillis) <=   76484) { RSTLT(); delay(6);Serial.print(3);delay(5); }               // Beat 135  STROBE COLOR
if ((runtime-offsetMillis) >=   77002 && (runtime-offsetMillis) <=   77005) { RSTLT(); delay(6);Serial.print(15);delay(5); }               // Beat 136  CENTERSPOT
if ((runtime-offsetMillis) >=   77522 && (runtime-offsetMillis) <=   77525) { }               // Beat 137
if ((runtime-offsetMillis) >=   78043 && (runtime-offsetMillis) <=   78046) { }               // Beat 138
if ((runtime-offsetMillis) >=   78563 && (runtime-offsetMillis) <=   78566) { RSTLT(); delay(6);Serial.print(3);delay(5); }              // Beat 139    STROBE COLOR
if ((runtime-offsetMillis) >=   79084 && (runtime-offsetMillis) <=   79087) { }               // Beat 140
if ((runtime-offsetMillis) >=   79605 && (runtime-offsetMillis) <=   79608) { RSTLT(); delay(6);Serial.print(15);delay(5); }              // Beat 141   CENTERSPOT
if ((runtime-offsetMillis) >=   80125 && (runtime-offsetMillis) <=   80128) { RSTLT(); delay(6);Serial.print(14);delay(5); }              // Beat 142   METEOR WHITE
if ((runtime-offsetMillis) >=   80646 && (runtime-offsetMillis) <=   80649) { }               // Beat 143
if ((runtime-offsetMillis) >=   81166 && (runtime-offsetMillis) <=   81169) { RSTLT(); delay(6);Serial.print(16);delay(5); }              // Beat 144   OUTSPOT
if ((runtime-offsetMillis) >=   81687 && (runtime-offsetMillis) <=   81690) { }               // Beat 145
if ((runtime-offsetMillis) >=   82208 && (runtime-offsetMillis) <=   82211) { RSTLT(); delay(6);Serial.print(3);delay(5); }             // Beat 146   STROBE COLOR
if ((runtime-offsetMillis) >=   82728 && (runtime-offsetMillis) <=   82731) { }               // Beat 147
if ((runtime-offsetMillis) >=   83249 && (runtime-offsetMillis) <=   83252) { RSTLT(); delay(6);Serial.print(15);delay(5); }         // Beat 148  CENTERSPOT
if ((runtime-offsetMillis) >=   83769 && (runtime-offsetMillis) <=   83772) { }               // Beat 149
if ((runtime-offsetMillis) >=   84290 && (runtime-offsetMillis) <=   84293) { }               // Beat 150
if ((runtime-offsetMillis) >=   84811 && (runtime-offsetMillis) <=   84814) { RSTLT(); delay(6);Serial.print(3);delay(5); }             // Beat 151  STROBE COLOR
if ((runtime-offsetMillis) >=   85331 && (runtime-offsetMillis) <=   85334) { RSTLT(); delay(6);Serial.print(15);delay(5); }            // Beat 152    CENTERSPOT
if ((runtime-offsetMillis) >=   85852 && (runtime-offsetMillis) <=   85855) { }               // Beat 153
if ((runtime-offsetMillis) >=   86372 && (runtime-offsetMillis) <=   86375) { }               // Beat 154
if ((runtime-offsetMillis) >=   86893 && (runtime-offsetMillis) <=   86896) { RSTLT(); delay(6);Serial.print(3);delay(5); }             // Beat 155  STROBE COLOR
if ((runtime-offsetMillis) >=   87414 && (runtime-offsetMillis) <=   87417) { RSTLT(); delay(6);Serial.print(15);delay(5); }            // Beat 156   CENTERSPOT
if ((runtime-offsetMillis) >=   87934 && (runtime-offsetMillis) <=   87937) { }               // Beat 157
if ((runtime-offsetMillis) >=   88455 && (runtime-offsetMillis) <=   88458) { }               // Beat 158
if ((runtime-offsetMillis) >=   88975 && (runtime-offsetMillis) <=   88978) { RSTLT(); delay(6);Serial.print(19);delay(5); }              // Beat 159   Meteor Green
if ((runtime-offsetMillis) >=   89496 && (runtime-offsetMillis) <=   89499) { RSTLT(); delay(6);Serial.print(16);delay(5); }              // Beat 160   OUTSPOT
if ((runtime-offsetMillis) >=   90017 && (runtime-offsetMillis) <=   90020) { }               // Beat 161
if ((runtime-offsetMillis) >=   90537 && (runtime-offsetMillis) <=   90540) { RSTLT(); delay(6);Serial.print(3);delay(5); }             // Beat 162   STROBE COLOR
if ((runtime-offsetMillis) >=   91058 && (runtime-offsetMillis) <=   91061) { }               // Beat 163
if ((runtime-offsetMillis) >=   91578 && (runtime-offsetMillis) <=   91581) { }               // Beat 164
if ((runtime-offsetMillis) >=   92099 && (runtime-offsetMillis) <=   92102) { RSTLT(); delay(6);Serial.print(12);delay(5); }             // Beat 165    THEATER CASE RAINBOW
if ((runtime-offsetMillis) >=   92620 && (runtime-offsetMillis) <=   92623) { }               // Beat 166
if ((runtime-offsetMillis) >=   93140 && (runtime-offsetMillis) <=   93143) { }               // Beat 167
if ((runtime-offsetMillis) >=   93661 && (runtime-offsetMillis) <=   93664) { }               // Beat 168
if ((runtime-offsetMillis) >=   94181 && (runtime-offsetMillis) <=   94184) { }               // Beat 169
if ((runtime-offsetMillis) >=   94702 && (runtime-offsetMillis) <=   94705) { }               // Beat 170
if ((runtime-offsetMillis) >=   95223 && (runtime-offsetMillis) <=   95226)  {  }               // Beat 171
if ((runtime-offsetMillis) >=   95743 && (runtime-offsetMillis) <=   95746)  {  }               // Beat 172
if ((runtime-offsetMillis) >=   96264 && (runtime-offsetMillis) <=   96267)  {  }               // Beat 173
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

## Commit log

2019-05-28 Add files via upload
    Files for animatronic eyes with LED RGB lighting an X and Y movement
    [Centerball Eye.stl, Centerball.FCStd, Final Eyeball w pupil.FCStd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]
2019-05-28 Add files via upload
    Files for servo board for animatronic skull with 4 servos for 3D printing
    Movements:
    Nodd motion
    Shake head motion
    Tilt motion
    Jaw motion
    [Final Bord.FCStd, Final Bord.stl, Servohalter Jaw.FCStd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]
2019-10-28 Add files via upload
    see readme
    [Arduino Code Translator.xlsx, Arduino Code Translator_ALPHA.xlsx, Arduino Code Translator_BETA.xlsx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]
2019-11-03 Add files via upload
    Arduino codes for animatronic skull
2019-11-03 Add files via upload
    Schematics for the animatronic skull
